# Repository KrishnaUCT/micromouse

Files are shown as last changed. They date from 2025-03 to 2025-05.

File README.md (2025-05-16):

# Project Description

This project focuses on the power subsystem of a micro mouse.

# Requirements
This section was extracted from the project description.

- Operate up to 4 motors bidirectionally with the pins available to you (listed in the power pinout
table). You will need to control 2x brushed DC motors which could each draw 200mA at the
highest voltage of a 1S1P battery (the battery is further specified in the battery section).
The other 2x motors are for the auxiliary connection and need to operate 500mA each.
- Place an INA219 for monitoring the battery on the I2C Bus and configure it correctly with
respect to the hardware (cannot have BOTH A0 AND A1 on GND)
- Charge the battery from the 9V input pin (listed in the power pinout table).
- Have two charging modes for a higher and lower charging current for the battery (200mA, and
approximately 600mA ±100mA from the battery perspective.
- Integrate USB C and get 9V out of the USB Host
- Provide 2x External Load Switching at 1A each (High Side connected to your 5V)
- Provide a 3V3 5% accuracy (300mA max) and 5V Out 5% accuracy (1.5A max)
- Provide an ON/OFF switch. OFF state: battery draw <30uA. ON state: can provide your robot
peak current of 2A. The switch needs to shut down 5V and 3V3.

# Usage

To view the source KiCAD filese, clone the repository and open in KiCAD v9.

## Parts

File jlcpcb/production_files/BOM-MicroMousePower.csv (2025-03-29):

Comment | Designator | Footprint | LCSC | Quantity
22u | C15,C8 | C_1206_3216Metric | C12891 | 2
2.2u | L1,L2,L3,L4,L5 | L_Cenker_CKCS4020 | C135262 | 5
10n | C4,C5,C6,C7 | C_0805_2012Metric | C15195 | 4
4.7u | C14,C2 | C_0402_1005Metric | C1569 | 2
10u | C1,C10,C11,C13,C9 | C_0805_2012Metric | C15850 | 5
10u | C12 | C_0805_2012Metric | C1634 | 1
USB_C_Receptacle_PowerOnly_6P | J1 | USB_C_Receptacle_GCT_USB4125-xx-x_6P_TopMnt_Horizontal | C168701 | 1
1.2k | R35 | R_0805_2012Metric | C17379 | 1
220k | R15 | R_0805_2012Metric | C17556 | 1
22k | R10,R11,R8 | R_0805_2012Metric | C17560 | 3
2k | R5 | R_0805_2012Metric | C17604 | 1
470 | R6 | R_0805_2012Metric | C17710 | 1
51k | R16,R34 | R_0805_2012Metric | C17737 | 2
300 | R3 | R_1206_3216Metric | C17887 | 1
100 | R18,R26 | R_1206_3216Metric | C17901 | 2
10k | R36,R37,R38,R9 | R_1206_3216Metric | C17902 | 4
10 | R19,R20,R22,R24,R25 | R_1206_3216Metric | C17903 | 5
AP62300WU | U8 | TSOT-23-6 | C1880390 | 1
BZT52C3V0S | D1,D2 | D_SOD-323 | C19077436 | 2
1 | R1,R12,R13,R30,R31,R32,R33,R39,R40,R41,R42,R43,R44 | R_0603_1608Metric | C22936 | 13
2M | R14 | R_0603_1608Metric | C22976 | 1
2 | R17,R23 | R_0201_0603Metric | C22977 | 2
4.7 | R21 | R_0603_1608Metric | C23164 | 1
3.3k | R4 | R_0805_2012Metric | C26010 | 1
1k | R7 | R_1206_3216Metric | C4410 | 1
10 | R2,R27,R28,R29,R45,R46,R47,R48 | R_1206_3216Metric | C47019 | 8
DRV8833PWPR | U4,U5 | TSSOP-16_4.4x5mm_P0.65mm | C50506 | 2
1u | C3,C52 | C_0402_1005Metric | C52923 | 2
MCP73831-3-MC | U2 | DFN-8-1EP_3x2mm_P0.5mm_EP1.7x1.4mm | C635038 | 1
TC1262-33 | U9 | SOT-223-3_TabPin2 | C638655 | 1
INA219AxDCN | U1 | SOT-23-8 | C87469 | 1
TPS61023DRLR | U6 | SOT-563 | C919459 | 1
TIP41C | Q1,Q2,Q3 | TO-220-3_Vertical | C92603 | 3
CH224K | U3 | SSOP-10-1EP_3.9x4.9mm_P1mm_EP2.1x3.3mm | C970725 | 1

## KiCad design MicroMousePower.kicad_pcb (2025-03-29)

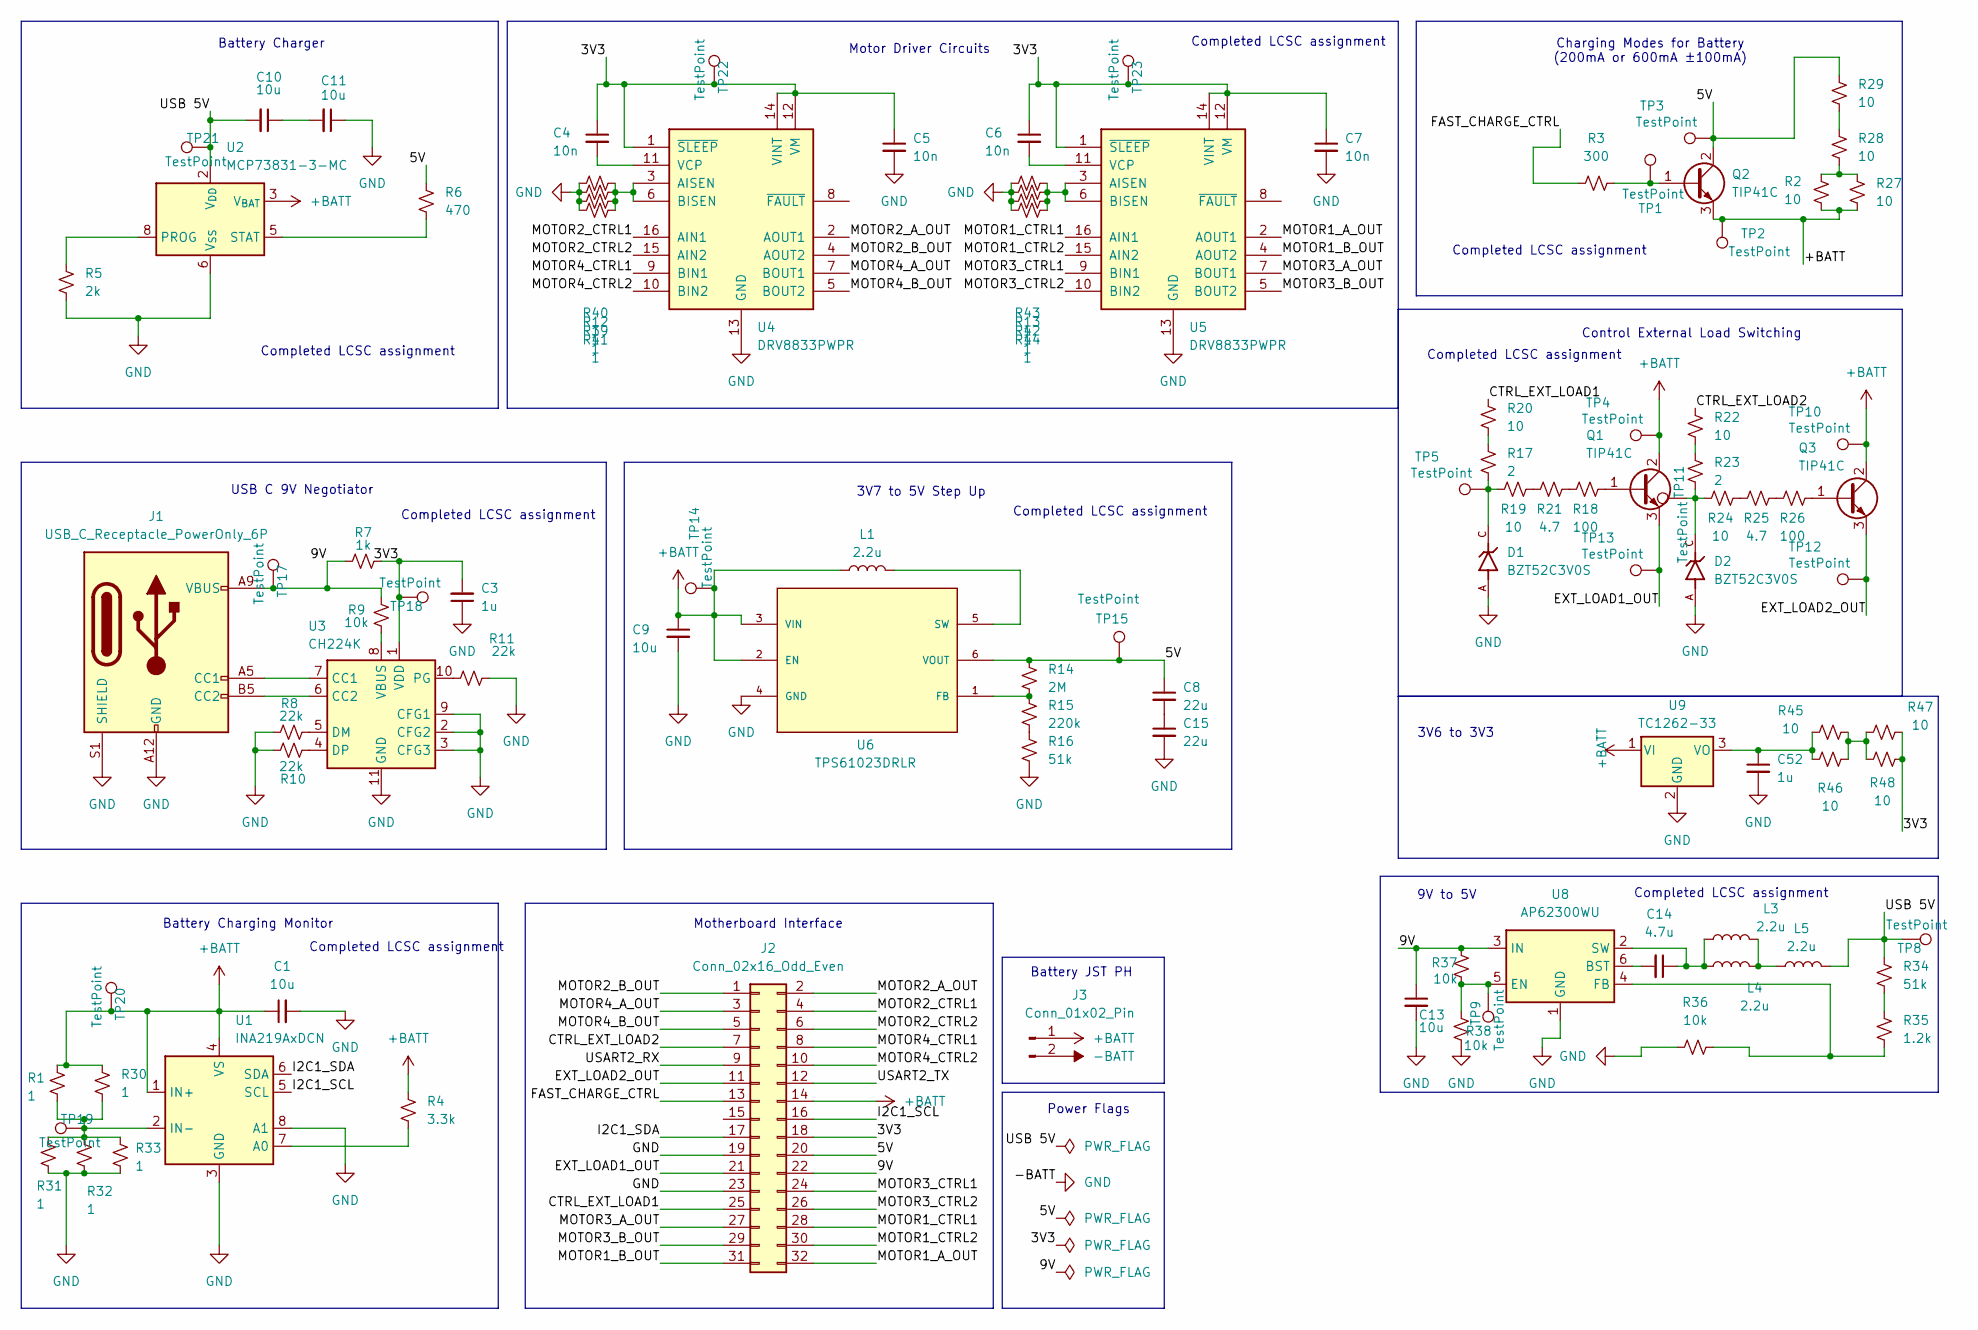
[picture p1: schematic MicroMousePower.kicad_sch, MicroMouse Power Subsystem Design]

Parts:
C1, C9, C10, C11, C13: 10u; C_0805_2012Metric; LCSC C15850
C3, C52: 1u; C_0402_1005Metric; LCSC C52923
C4, C5, C6, C7: 10n; C_0805_2012Metric; LCSC C15195
C8, C15: 22u; C_1206_3216Metric; LCSC C12891
C14: 4.7u; C_0402_1005Metric; LCSC C1569
D1, D2: BZT52C3V0S; D_SOD-323; PARTREV H2212; LCSC C19077436
J1: USB_C_Receptacle_PowerOnly_6P; USB_C_Receptacle_GCT_USB4125-xx-x_6P_TopMnt_Horizontal; LCSC C168701
J2: Conn_02x16_Odd_Even; PinHeader_2x16_P2.54mm_Vertical; LCSC C5307343
J3: Conn_01x02_Pin; JST_PH_B2B-PH-K_1x02_P2.00mm_Vertical; LCSC C131337
L1, L3, L4, L5: 2.2u; L_Cenker_CKCS4020; LCSC C135262
Q1, Q2, Q3: TIP41C; TO-220-3_Vertical; LCSC C92603
R1, R12, R13, R30, R31, R32, R33, R39, R40, R41, R42, R43, R44: 1; R_0603_1608Metric; LCSC C22936
R2, R27, R28, R29, R45, R46, R47, R48: 10; R_1206_3216Metric; LCSC C47019
R3: 300; R_1206_3216Metric; LCSC C17887
R4: 3.3k; R_0805_2012Metric; LCSC C26010
R5: 2k; R_0805_2012Metric; LCSC C17604
R6: 470; R_0805_2012Metric; LCSC C17710
R7: 1k; R_1206_3216Metric; LCSC C4410
R8, R10: 22k; R_0805_2012Metric; LCSC C17560
R9, R36, R37, R38: 10k; R_1206_3216Metric; LCSC C17902
R11: 22k; R_0805_2012Metric; LCSCf C17560
R14: 2M; R_0603_1608Metric; LCSC C22976
R15: 220k; R_0805_2012Metric; LCSC C17556
R16, R34: 51k; R_0805_2012Metric; LCSC C17737
R17, R23: 2; R_0201_0603Metric; LCSC C22977
R18, R26: 100; R_1206_3216Metric; LCSC C17901
R19, R20, R22, R24: 10; R_1206_3216Metric; LCSC C17903
R21: 4.7; R_0603_1608Metric; LCSC C23164
R25: 4.7; R_0603_1608Metric; LCSC C17903
R35: 1.2k; R_0805_2012Metric; LCSC C17379
TP1, TP2, TP3, TP4, TP5, TP8, TP9, TP10, TP11, TP12, TP13, TP14, TP15, TP17, TP18, TP19, TP20, TP21, TP22, TP23: TestPoint; TestPoint_Pad_D1.0mm
U1: INA219AxDCN; SOT-23-8; LCSC C87469
U2: MCP73831-3-MC; DFN-8-1EP_3x2mm_P0.5mm_EP1.7x1.4mm; LCSC C635038
U3: CH224K; SSOP-10-1EP_3.9x4.9mm_P1mm_EP2.1x3.3mm; LCSC C970725
U4, U5: DRV8833PWPR; TSSOP-16_4.4x5mm_P0.65mm; LCSC C50506
U6: TPS61023DRLR; SOT-563; MANUFACTURER_PART_NUMBER TPS61023DRLR; DigiKey_Part_Number 296-TPS61023DRLRTR-ND
U8: AP62300WU; TSOT-23-6; LCSC C1880390
U9: TC1262-33; SOT-223-3_TabPin2; LCSC C638655

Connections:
+BATT: C1.1, C9.1, J2.14, J3.1, L1.1, Q1.2 (C), Q2.3 (E), Q3.2 (C), R1.1, R2.2, R4.1, R27.2, R30.1, TP2.1, TP4.1, TP10.1, TP14.1, TP20.1, U1.1 (IN+), U1.4 (VS), U2.3 (V_{BAT}), U2.4 (V_{BAT}), U6.2 (EN), U6.3 (VIN), U9.1 (VI); also elsewhere on the board
-BATT: C1.2, C3.1, C5.2, C7.2, C9.2, C11.1, C13.2, C15.2, C52.2, D1.A, D2.A, J1.A12 (GND), J1.B12 (GND), J1.S1 (SHIELD), J2.19, J2.23, J3.2, R5.2, R8.1, R10.2, R11.2, R12.1, R13.1, R16.2, R31.2, R32.2, R33.2, R36.1, R38.1, R39.1, R40.1, R41.1, R42.1, R43.1, R44.1, U1.3 (GND), U1.8 (A1), U2.6 (V_{SS}), U3.2 (CFG2), U3.3 (CFG3), U3.9 (CFG1), U3.11 (GND), U4.13 (GND), U5.13 (GND), U6.4 (GND), U8.1 (GND), U9.2 (GND); also elsewhere on the board
/3V3: C3.2, C4.1, C5.1, C6.1, C7.1, J2.18, R7.2, R47.2, R48.2, TP18.1, TP22.1, TP23.1, U3.1 (VDD), U4.1 (~SLEEP), U4.12 (VM), U4.14 (VINT), U5.1 (~SLEEP), U5.12 (VM), U5.14 (VINT); also elsewhere on the board
/5V: C8.1, J2.20, Q2.2 (C), R6.1, R14.1, R29.1, TP3.1, TP15.1, U6.6 (VOUT)
/9V: C13.1, J1.A9 (VBUS), J1.B9 (VBUS), J2.22, R7.1, R9.1, R37.2, TP17.1, U8.3 (IN)
/CTRL_EXT_LOAD1: J2.25, R20.1
/CTRL_EXT_LOAD2: J2.7, R22.1
/EXT_LOAD1_OUT: J2.21, Q1.3 (E), TP13.1
/EXT_LOAD2_OUT: J2.11, Q3.3 (E), TP12.1
/FAST_CHARGE_CTRL: J2.13, R3.1
/I2C1_SCL: J2.16, U1.5 (SCL)
/I2C1_SDA: J2.17, U1.6 (SDA)
/MOTOR1_A_OUT: J2.32, U5.2 (AOUT1)
/MOTOR1_B_OUT: J2.31, U5.4 (AOUT2)
/MOTOR1_CTRL1: J2.28, U5.16 (AIN1)
/MOTOR1_CTRL2: J2.30, U5.15 (AIN2)
/MOTOR2_A_OUT: J2.2, U4.2 (AOUT1)
/MOTOR2_B_OUT: J2.1, U4.4 (AOUT2)
/MOTOR2_CTRL1: J2.4, U4.16 (AIN1)
/MOTOR2_CTRL2: J2.6, U4.15 (AIN2)
/MOTOR3_A_OUT: J2.27, U5.7 (BOUT1)
/MOTOR3_B_OUT: J2.29, U5.5 (BOUT2)
/MOTOR3_CTRL1: J2.24, U5.9 (BIN1)
/MOTOR3_CTRL2: J2.26, U5.10 (BIN2)
/MOTOR4_A_OUT: J2.3, U4.7 (BOUT1)
/MOTOR4_B_OUT: J2.5, U4.5 (BOUT2)
/MOTOR4_CTRL1: J2.8, U4.9 (BIN1)
/MOTOR4_CTRL2: J2.10, U4.10 (BIN2)
/USART2_RX: J2.9
/USART2_TX: J2.12
/USB 5V: C10.2, L5.2, R34.1, TP8.1, TP21.1, U2.1 (V_{DD}), U2.2 (V_{DD})
unnamed: C10.1, C11.2
unnamed: C8.2, C15.1
unnamed: D1.C, R17.2, R19.1, TP5.1
unnamed: D2.C, R23.2, R24.1, TP11.1
unnamed: J1.A5 (CC1), U3.7 (CC1)
unnamed: J1.B5 (CC2), U3.6 (CC2)
unnamed: L3.2, L4.2, L5.1
unnamed: Q1.1 (B), R18.2
unnamed: Q2.1 (B), R3.2, TP1.1
unnamed: Q3.1 (B), R26.2
unnamed: R2.1, R27.1, R28.2
unnamed: R15.2, R16.1
unnamed: R17.1, R20.2
unnamed: R18.1, R21.2
unnamed: R19.2, R21.1
unnamed: R22.2, R23.1
unnamed: R24.2, R25.1
unnamed: R25.2, R26.1
unnamed: R28.1, R29.2
unnamed: R34.2, R35.1
unnamed: R45.2, R46.2, R47.1, R48.1
unnamed: R4.2, U1.7 (A0)
unnamed: R1.2, R30.2, R31.1, R32.1, R33.1, TP19.1, U1.2 (IN-)
unnamed: R5.1, U2.8 (PROG)
unnamed: R6.2, U2.5 (STAT)
unnamed: R8.2, U3.5 (DM)
unnamed: R10.1, U3.4 (DP)
unnamed: R11.1, U3.10 (PG)
unnamed: R9.2, U3.8 (VBUS)
unnamed: R12.2, R39.2, R40.2, R41.2, U4.3 (AISEN), U4.6 (BISEN)
unnamed: C4.2, U4.11 (VCP)
unnamed: R13.2, R42.2, R43.2, R44.2, U5.3 (AISEN), U5.6 (BISEN)
unnamed: C6.2, U5.11 (VCP)
unnamed: R14.2, R15.1, U6.1 (FB)
unnamed: L1.2, U6.5 (SW)
unnamed: C14.2, U8.6 (BST)
unnamed: R37.1, R38.2, TP9.1, U8.5 (EN)
unnamed: R35.2, R36.2, U8.4 (FB)
unnamed: C14.1, L3.1, L4.1, U8.2 (SW)
unnamed: C52.1, R45.1, R46.1, U9.3 (VO)

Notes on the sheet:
Battery Charging Monitor
Completed LCSC assignment
Power Flags
Motor Driver Circuits
3V6 to 3V3
Charging Modes for Battery (200mA or 600mA ±100mA)
Battery JST PH
USB C 9V Negotiator
9V to 5V
3V7 to 5V Step Up
Motherboard Interface
Battery Charger
Control External Load Switching

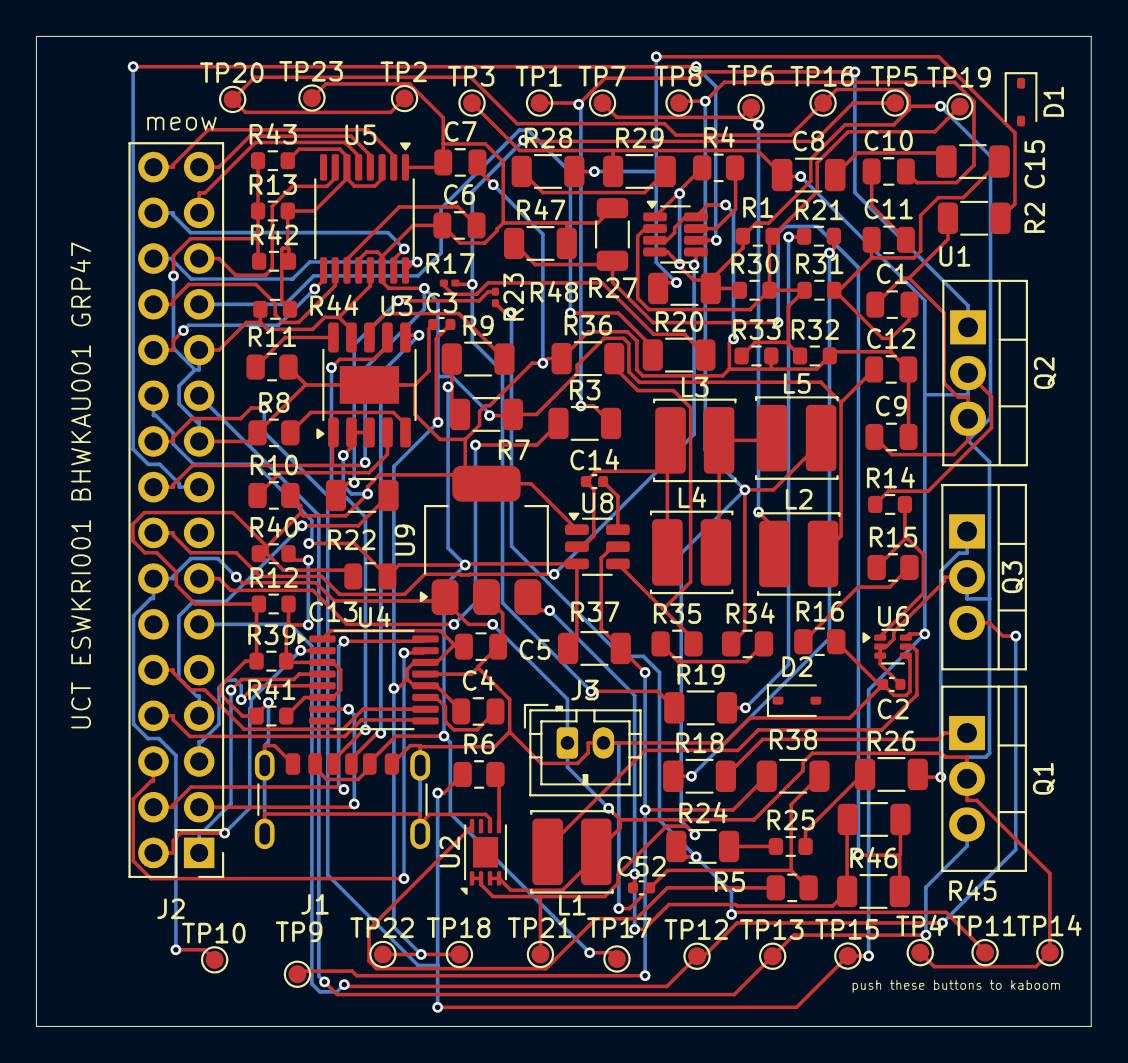
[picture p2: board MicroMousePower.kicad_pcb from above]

Board: 2 copper layers, 58.6 x 55.0 mm, 108 parts (0 on the bottom side), 70 nets.

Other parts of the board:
C2: 4.7u; C_0402_1005Metric
C12: 10u; C_0805_2012Metric
L2: 2.2u; L_Cenker_CKCS4020
TP6, TP7, TP16: TestPoint; TestPoint_Pad_D1.0mm

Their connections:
+BATT: C2.2, TP16.1; also elsewhere on the board
-BATT: C2.1, C12.2; also elsewhere on the board
/3V3: C12.1, L2.2; also elsewhere on the board
unnamed: L2.1, TP6.1, TP7.1

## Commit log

2025-03-22 init: empty project
    [MicroMousePower.kicad_pcb, MicroMousePower.kicad_sch]
2025-03-22 r with comment
    [MicroMousePower.kicad_sch]
2025-03-22 (text "higher and lower charging current for the battery (200mA or 600mA ±100mA)"
    not sure about how its gonna be connected later,just uploaded schematic
    [MicroMousePower.kicad_sch]
2025-03-24 completed INA219 integration
    [MicroMousePower.kicad_sch]
2025-03-24 added battery charging circuit
    [MicroMousePower.kicad_sch]
2025-03-24 checking if it works
    [MicroMousePower.kicad_sch]
2025-03-27 organized circuit sections, added schematic metadata
    [MicroMousePower.kicad_sch]
2025-03-27 integrated USB C 9V negotiator
    [MicroMousePower.kicad_sch]
2025-03-27 defined motherboard interface and added motor driver IC
    [MicroMousePower.kicad_sch]
2025-03-27 connected motor driver circuit
    [MicroMousePower.kicad_sch]
2025-03-27 power flag defintions for ERC
    [MicroMousePower.kicad_sch]
2025-03-27 template for step down IC
    [MicroMousePower.kicad_sch]
2025-03-27 added 3V6 to 3V3 step down
    [MicroMousePower.kicad_sch]
2025-03-27 added current sources
    [MicroMousePower.kicad_sch]
2025-03-28 added LCSC values to all components
    [MicroMousePower.kicad_sch]
2025-03-28 completed schematic with LCSC codes
    [MicroMousePower.kicad_sch]
2025-03-28 fixed ERC errors
    [MicroMousePower.kicad_sch]
2025-03-28 fixed more ERC errors
    [MicroMousePower.kicad_sch]
2025-03-28 meow idk?
    pss pss
    [MicroMousePower.kicad_sch]
2025-03-28 added testpoints
    [MicroMousePower.kicad_sch]
2025-03-28 fixed misc oversights and assigned footprints
    [MicroMousePower.kicad_pcb, MicroMousePower.kicad_sch]
2025-03-28 added missing LCSC codes
    [MicroMousePower.kicad_sch]
2025-03-28 fixed yet another mislabeled LCSC code
    [MicroMousePower.kicad_sch]
2025-03-28 tried my best lol
    dont forget on WA
    [CPL-MicroMousePower.csv, MicroMousePower-CuBottom.gbr, MicroMousePower-CuTop.gbr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]
2025-03-28 try 2
    try ?
    [MicroMousePower.kicad_pcb]
2025-03-28 updated pinheader footprint
    [MicroMousePower.dsn, MicroMousePower.kicad_pcb, MicroMousePower.kicad_sch]
2025-03-28 rearranged pcb layout
    [MicroMousePower.kicad_pcb, MicroMousePowervF.dsn]
2025-03-28 moved tips
    [MicroMousePower.kicad_pcb, MicroMousePowerFinal.dsn]
2025-03-28 rotated for bending
    [MicroMousePower.kicad_pcb, MicroMousePowerFinalFinal.dsn]
2025-03-28 moved resistors to overcome disconnect
    [MicroMousePower.kicad_pcb]
2025-03-28 exported fv4
    [MicroMousePowerFV4.dsn]
2025-03-28 fixed another disconnect
    [MicroMousePower.kicad_pcb, MicroMousePowerFV5.dsn]
2025-03-28 completed final routing and generated JLCPCB production files
    [BOM-MicroMousePower.csv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]
2025-03-28 updated schematic due to ordering error
    [MicroMousePower.kicad_pcb, MicroMousePower.kicad_sch]
2025-03-28 the pain never ends
    [CPL-MicroMousePower.csv, MicroMousePower-CuBottom.gbr, MicroMousePower-CuTop.gbr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]
2025-03-28 there is light at the end
    [BOM-MicroMousePower.csv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]
2025-03-29 final submission
    [BOM-MicroMousePower.csv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]
2025-03-29 deleted routing iterations
    [MicroMousePower.dsn, MicroMousePowerFV10.dsn, MicroMousePowerFV11.dsn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]
2025-04-23 cleaned up schematic
    [MicroMousePower.kicad_sch]
2025-05-16 added comments
    [MicroMousePower.kicad_sch]

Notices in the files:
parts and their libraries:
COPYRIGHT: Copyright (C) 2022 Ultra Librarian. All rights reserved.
